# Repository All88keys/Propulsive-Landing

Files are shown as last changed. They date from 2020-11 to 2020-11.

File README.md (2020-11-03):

# propulsive-landing
 Arduino Script for HERMES rocket tests

## v0
Test scripts for LEMNOS3 board for Hermes I ("Agon0")

## v1
Test scripts for LEMNOS3 board for Hermes I ("Agon1")

## LEMNOS3
Autodesk EAGLE project for LEMNOS3, logic board design for Hermes I. 
- [Link to EAGLE download](https://www.autodesk.com/products/eagle/overview?plc=F360&term=1-YEAR&support=ADVANCED&quantity=1)
- [Link to MPU 6050](https://www.sparkfun.com/products/11028)

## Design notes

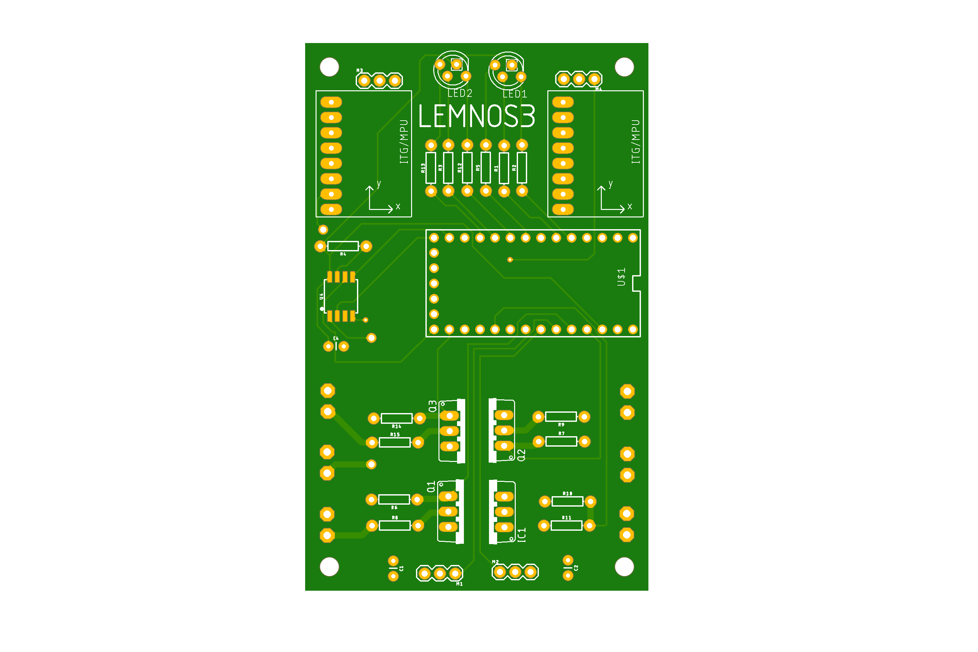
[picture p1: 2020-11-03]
LEMNOS3.png

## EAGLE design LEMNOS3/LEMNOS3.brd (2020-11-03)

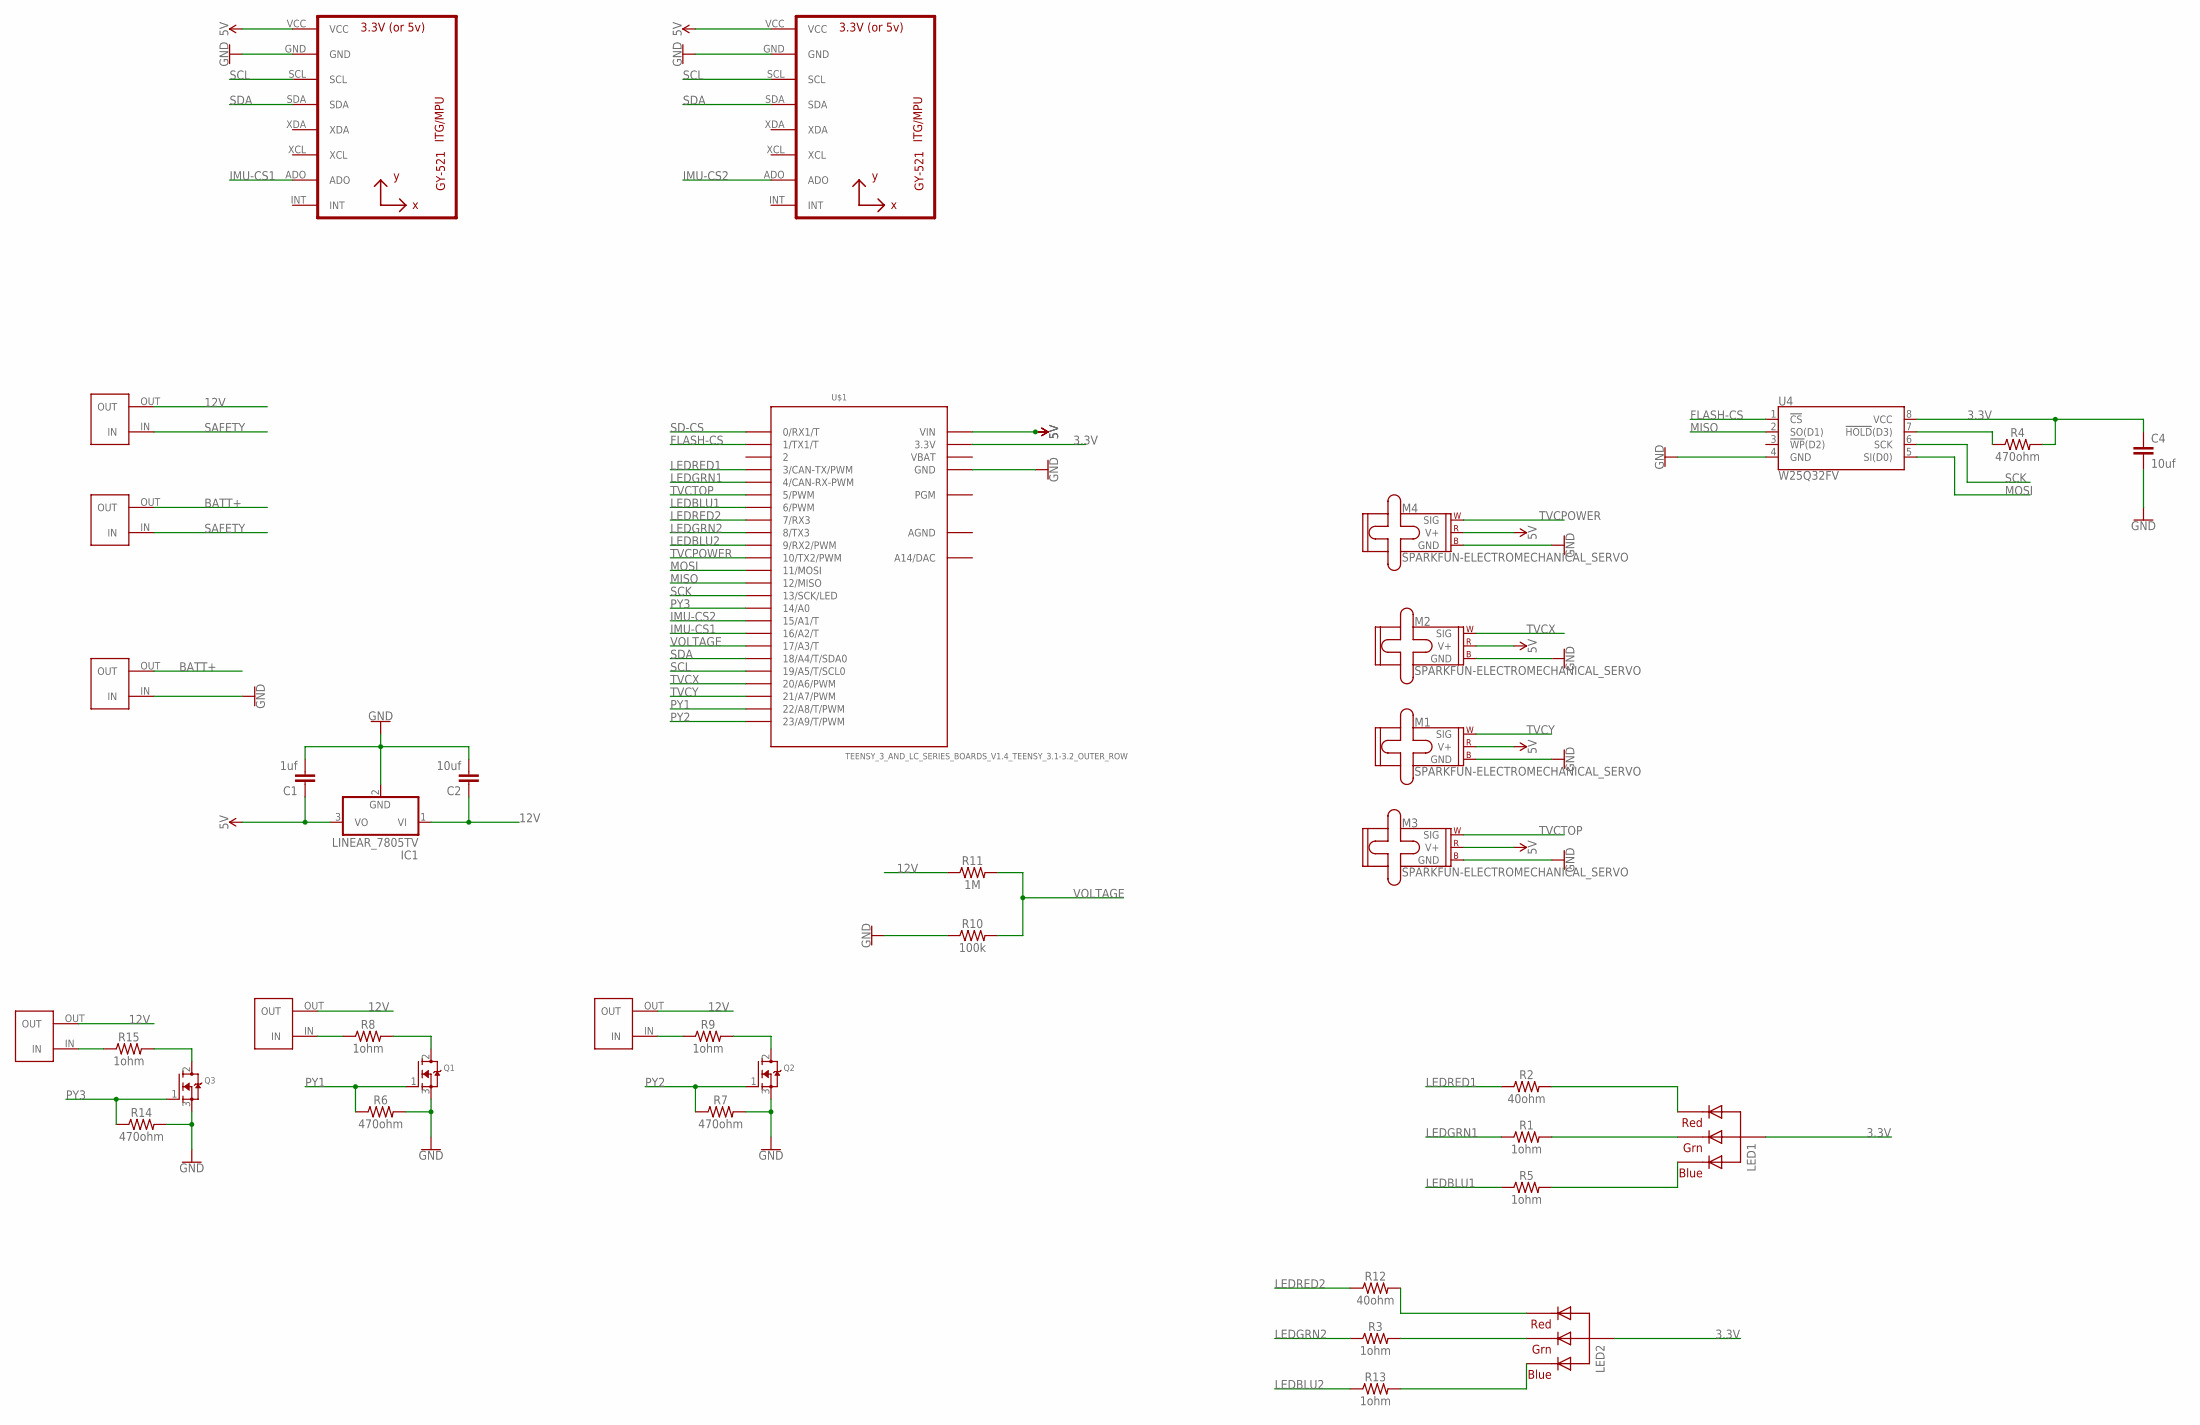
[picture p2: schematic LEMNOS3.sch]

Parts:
C1: 1uf; SPARKFUN-CAPACITORS_CAP-PTH-2.54
C2, C4: 10uf; SPARKFUN-CAPACITORS_CAP-PTH-2.54
IC1: LINEAR_7805TV; LINEAR_TO220V
LED1, LED2: RGBLED_CA-5MM; LED5MMRGB
M1, M2, M3, M4: SPARKFUN-ELECTROMECHANICAL_SERVO; SPARKFUN-ELECTROMECHANICAL_1X03
Q1, Q2, Q3: ADAFRUIT_MOSFET-NGDS_TO220V; ADAFRUIT_TO220V
R1, R3, R5, R8, R9, R13, R15: 1ohm; SPARKFUN-RESISTORS_AXIAL-0.3
R2, R12: 40ohm; SPARKFUN-RESISTORS_AXIAL-0.3
R4, R6, R7, R14: 470ohm; SPARKFUN-RESISTORS_AXIAL-0.3
R10: 100k; SPARKFUN-RESISTORS_AXIAL-0.3
R11: 1M; SPARKFUN-RESISTORS_AXIAL-0.3
U1, U2: GY-521_GY-521MPU6050; GY-521_GY-521
U4: W25Q32FV; SPARKFUN-IC-MEMORY_SOIC-8
U$1: TEENSY_3_AND_LC_SERIES_BOARDS_V1.4_TEENSY_3.1-3.2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; TEENSY_3_AND_LC_SERIES_BOARDS_V1.4_TEENSY_3.0-3.2&LC_OUTER_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
U$2, U$3, U$4, U$5, U$6, U$8: BLACKTERMBLOCK_BLACKTERMBLOCK

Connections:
3.3V: C4.1, LED1.2 (VCC), LED2.2 (VCC), R4.P$2 (2), U4.8 (VCC), U$1.3.3V, U$1.3.3V1 (3.3V)
5V: C1.1, IC1.3 (VO), M1.2 (V+), M2.2 (V+), M3.2 (V+), M4.2 (V+), U1.VCC, U2.VCC, U$1.VIN
12V: C2.1, IC1.1 (VI), R11.P$1 (1), U$2.OUT, U$5.OUT, U$6.OUT, U$8.OUT
AGND: U$1.AGND
BATT+: U$3.OUT, U$4.OUT
FLASH-CS: U4.1 (!CS!), U$1.1 (1/TX1/T)
GND: C1.2, C2.2, C4.2, IC1.2 (GND), M1.3 (GND), M2.3 (GND), M3.3 (GND), M4.3 (GND), Q1.3 (S), Q2.3 (S), Q3.3 (S), R6.P$2 (2), R7.P$2 (2), R10.P$1 (1), R14.P$2 (2), U1.GND, U2.GND, U4.4 (GND), U$1.GND, U$1.GND1 (GND), U$3.IN
IMU-CS1: U1.ADO, U$1.16/A2 (16/A2/T)
IMU-CS2: U2.ADO, U$1.15/A1 (15/A1/T)
LEDBLU1: R5.P$1 (1), U$1.6 (6/PWM)
LEDBLU2: R13.P$1 (1), U$1.9 (9/RX2/PWM)
LEDGRN1: R1.P$1 (1), U$1.4 (4/CAN-RX-PWM)
LEDGRN2: R3.P$1 (1), U$1.8 (8/TX3)
LEDRED1: R2.P$1 (1), U$1.3 (3/CAN-TX/PWM)
LEDRED2: R12.P$1 (1), U$1.7 (7/RX3)
MISO: U4.2 (SO(D1)), U$1.12 (12/MISO)
MOSI: U4.5 (SI(D0)), U$1.11 (11/MOSI)
unnamed: R15.P$1 (1), U$2.IN
unnamed: LED1.1 (RED), R2.P$2 (2)
unnamed: R4.P$1 (1), U4.7 (!HOLD!(D3))
unnamed: LED1.3 (GREEN), R1.P$2 (2)
unnamed: LED1.4 (BLUE), R5.P$2 (2)
unnamed: R8.P$1 (1), U$5.IN
unnamed: Q1.2 (D), R8.P$2 (2)
unnamed: LED2.1 (RED), R12.P$2 (2)
unnamed: R9.P$1 (1), U$6.IN
unnamed: Q2.2 (D), R9.P$2 (2)
unnamed: LED2.3 (GREEN), R3.P$2 (2)
unnamed: LED2.4 (BLUE), R13.P$2 (2)
unnamed: Q3.2 (D), R15.P$2 (2)
PY1: Q1.1 (G), R6.P$1 (1), U$1.22/A8 (22/A8/T/PWM)
PY2: Q2.1 (G), R7.P$1 (1), U$1.23/A9 (23/A9/T/PWM)
PY3: Q3.1 (G), R14.P$1 (1), U$1.14/A0
SAFETY: U$4.IN, U$8.IN
SCK: U4.6 (SCK), U$1.13 (13/SCK/LED)
SCL: U1.SCL, U2.SCL, U$1.19/A5 (19/A5/T/SCL0)
SD-CS: U$1.0 (0/RX1/T)
SDA: U1.SDA, U2.SDA, U$1.18/A4 (18/A4/T/SDA0)
TVCPOWER: M4.1 (SIG), U$1.10 (10/TX2/PWM)
TVCTOP: M3.1 (SIG), U$1.5 (5/PWM)
TVCX: M2.1 (SIG), U$1.20/A6 (20/A6/PWM)
TVCY: M1.1 (SIG), U$1.21/A7 (21/A7/PWM)
VBAT: U$1.VBAT
VOLTAGE: R10.P$2 (2), R11.P$2 (2), U$1.17/A3 (17/A3/T)

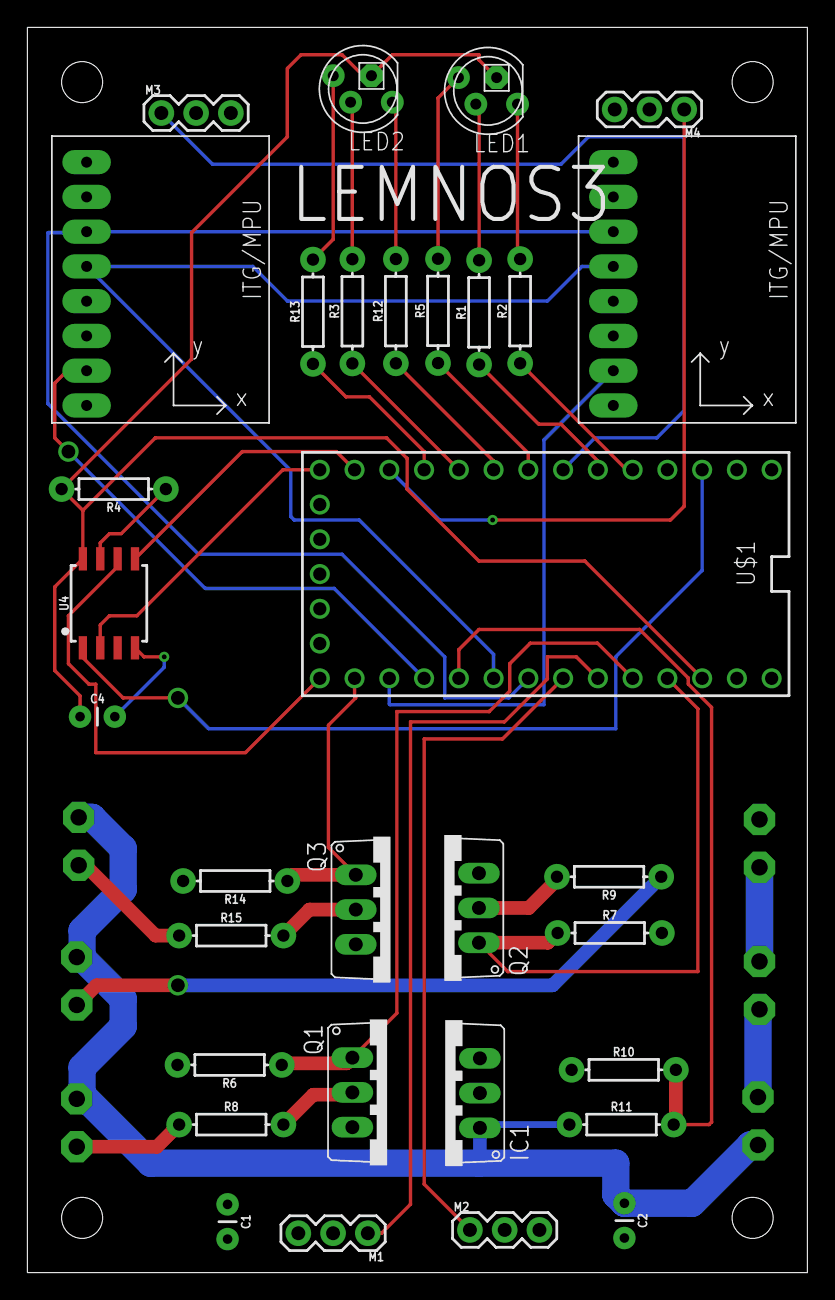
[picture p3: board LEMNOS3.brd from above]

Board: 2 copper layers, 57.0 x 91.0 mm, 38 parts (0 on the bottom side), 41 nets.

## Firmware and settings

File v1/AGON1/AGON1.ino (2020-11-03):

//includes
#include "I2Cdev.h"     //I2C protocol
#include "MPU6050.h"    //imu
#include "Wire.h"
#include <Eigen313.h>
//#include <stlport.h>
//#include <Eigen30.h>
using namespace Eigen;
#include <LU>
#include <SD.h>
#include<SPIFlash.h>
#include <Servo.h>

long MEGA=1000000;
long pi=31416;

//modes
int n=0;
int c=0;

//clock
long t0;
long t;
long h;

//mission parameters
long tb=.5*MEGA;
long tbEstDelay=.25*MEGA;
long setupWait=60; //120
long warningWait=60;  //120
long warning2Wait=30;  //30
long countdownWait=10; //10
long calibrateTime=0;

float dropTBuffer=.05*MEGA;
long dropBuffer=3276/8;  //~1 m/s^2
long dropGoal=-32768/8; //-g

float fireTBuffer=.05*MEGA;
float fireBuffer=3276/4/8; //~.25 m/s^2
float fireGoal=-32768/8; //-g

float landTBuffer=.5*MEGA;
float landBuffer=3276/2/8; //
float landGoal=0;

//mision variables
long dropT;
long dropTime;
long fireTime;
long landTime;
bool buffStatus;
float buffCountDown;
//float accAvg;
//float accCount;

//get accel, process y
int16_t ax, ay, az;
int16_t gx, gy, gz;
long offsets [3];
long O1, O2, O3;
int imuRange=32768;         //range of raw values that accelerometer will output
int aSensitivity=8;         //how many g's represented in that range
int gSensitivity=250;
float aMult=imuRange/9.81/aSensitivity;
//long gMult=imuRange/gSensitivity*180/pi*10000;
float gMult=imuRange/gSensitivity;
MPU6050 imu;
long yaw;

//controller
MatrixXf Ka(2,6);
VectorXi x(6); 
VectorXf xControl(6); 
VectorXf ua(2);
float ub [2];
float uc [2];
MatrixXi A [9];
MatrixXi B [9];
float maxU=5*3.14159/180;
long uLast [2]={0, 0};

//TVC
int TVC_TOP_PIN = 5;
int TVC_X_PIN = 20;
int TVC_Y_PIN = 21;
Servo tvcTop;
Servo tvcX;
Servo tvcY;
int tvcXoffset=85;
int tvcYoffset=83;
float beta=.6;
int gear=9;
float damper=1.5;
int tvcDelay=10;

//pyro
int pyroPin = 22;

//blink
int B_LED_1 = 6;
int G_LED_1 = 4;
int B_LED_2 = 9;
int G_LED_2 = 8;
//each pattern has 9 values
//0: Hz
//1-4: A, command for each, green1, blue1, green2, blue2,
//5-8: B, command for each
int blink0 [] ={1, 1, 0, 1, 0, 1, 0, 1, 0};
int blink1 [] ={1, 0, 1, 0, 1, 0, 1, 0, 1};
int blink2 [] ={1, 0, 1, 0, 1, 1, 0, 1, 0};
int blink3 [] ={1, 1, 0, 1, 0, 0, 0, 0, 0};
int blink4 [] ={1, 0, 0, 0, 0, 0, 0, 0, 0};
int blink5 [] ={1, 0, 1, 0, 1, 0, 1, 0, 1};
int blink6 [] ={1, 0, 0, 0, 0, 0, 0, 0, 0};
int blink7 [] ={1, 1, 0, 1, 0, 1, 0, 1, 0};
int blink8 [] ={1, 0, 1, 0, 1, 1, 0, 1, 0};
int blink9 [] ={1, 0, 1, 0, 1, 0, 1, 0, 1};
int blinkMaster [90];
int blinkCommand;
long nextBlink;
bool blinkFlag=false;

long dispGap=100000;
long nextDisplay=dispGap;

#define CHIPSIZE MB64
SPIFlash flash(1);


void setup() {

    pinMode(G_LED_1, OUTPUT);
    pinMode(B_LED_1, OUTPUT);
    pinMode(G_LED_2, OUTPUT);
    pinMode(B_LED_2, OUTPUT);
    
    digitalWrite(G_LED_1, LOW);
    digitalWrite(B_LED_1, LOW);
    digitalWrite(G_LED_2, LOW);
    digitalWrite(B_LED_2, LOW);
    
    // accel, processY
    // join I2C bus (I2Cdev library doesn't do this automatically)
    #if I2CDEV_IMPLEMENTATION == I2CDEV_ARDUINO_WIRE
        Wire.begin();
    #elif I2CDEV_IMPLEMENTATION == I2CDEV_BUILTIN_FASTWIRE
        Fastwire::setup(400, true);
    #endif
    

    flash.begin(9600);
    //flash.eraseChip();

    tvcX.attach(TVC_X_PIN);
    tvcY.attach(TVC_Y_PIN);
    tvcTop.attach(TVC_TOP_PIN);

    tvcTop.write(10); delay(1000);
    tvc(0, 0, beta, tvcDelay*100);
    tvc(30, 0, beta, tvcDelay*100);
    tvc(-30, 0, beta, tvcDelay*100);
    tvc(0, 0, beta, tvcDelay*100);
    tvc(0, 30, beta, tvcDelay*100);
    tvc(0, -30, beta, tvcDelay*100);
    tvc(0, 0, beta, tvcDelay*100);
    
    
  //blink
    for (int i=0; i<9; i++){
      blinkMaster[i+9*0]=blink0[i]; blinkMaster[i+9*1]=blink1[i];
      blinkMaster[i+9*2]=blink2[i]; blinkMaster[i+9*3]=blink3[i];
      blinkMaster[i+9*4]=blink4[i]; blinkMaster[i+9*5]=blink5[i];
      blinkMaster[i+9*6]=blink6[i]; blinkMaster[i+9*7]=blink7[i];
      blinkMaster[i+9*8]=blink8[i]; blinkMaster[i+9*9]=blink9[i];
    }

  pinMode(pyroPin, OUTPUT);
  digitalWrite(pyroPin, LOW);
    
  x<<0,0,0,0,0,0;
  Ka<<0.34641, 1.72254, 0.32694, 0, 0, 0, 0, 0, 0, 0.34641, -1.88376, -0.3991;
  n=0;
  t=0;
}

void loop() {

  //clk update
  
  t=micros();
  h=t-t0;
  t0=t;

  // check state
  switch(n){
    case 0: //setup and idle  &&& green
      if (t>setupWait*MEGA){
        n++; blinkFlag=true;
      }
    break;
    case 1: //warning  &&&   blue
      if (t>(setupWait+warningWait)*MEGA){
        n++; blinkFlag=true;
        //imu.CalibrateGyro(20);
        //imu.CalibrateAccel(50);
      }
    break;
    case 2: //clear the pad, calibrate   &&&   blue/green
      if (t>(setupWait+warningWait+warning2Wait)*MEGA){
        n++; blinkFlag=true;

          digitalWrite(G_LED_1, LOW);
          digitalWrite(B_LED_1, LOW);
          digitalWrite(G_LED_2, LOW);
          digitalWrite(B_LED_2, LOW);
          
          imu.initialize();
          imu.setFullScaleGyroRange(MPU6050_GYRO_FS_250);
          imu.setFullScaleAccelRange(MPU6050_ACCEL_FS_8);
          imu.CalibrateGyro(30); // Fine tune after setting offsets with less Loops.
          imu.CalibrateAccel(30);
      
          Serial.print(">");
          long aSums [3]={0,0,0};
          //float offsets
          for (int i=0; i<10; i++){
            for (int j=0; j<250; j++){
              imu.getMotion6(&ax, &az, &ay, &gx, &gz, &gy);
              aSums[0]+=ax;
              aSums[1]+=ay;
              aSums[2]+=az; 
      
            }
            Serial.print(".");
            delay(500);
          }
          Serial.println();
          for (int i=0; i<3; i++){
            aSums[i]/=2500;
            //Serial.println(aSums[i]);
          }
      
          offsets[0]=aSums[0];
          offsets[1]=aSums[1]-imuRange/2;
          offsets[2]=aSums[2];            

          calibrateTime=micros();
      }
    break;
    case 3: //countdown   &&&   green//off
      if (t>calibrateTime+countdownWait*MEGA){
        n++; blinkFlag=true;
        buffStatus=false; buffCountDown=dropTBuffer;
        tvcTop.write(150); delay(150);
        dropT=micros();
      }
    break;
    case 4: //drop   &&&   nothing
      if(az<dropGoal+dropBuffer){
        if (buffStatus){buffCountDown-=h; }
        else{buffStatus=true;}
      }
      else{
        if (buffStatus){buffStatus=false; buffCountDown=dropTBuffer; }
      }
      if ((buffCountDown<0) || (t>dropT+MEGA*.25)){
        dropTime=t-dropTBuffer;
        buffStatus=false; buffCountDown=dropTBuffer;
        //accAvg=0;accCount=0;
        n++; blinkFlag=true;
      }
    break;
    case 5: //ballistic (control tvc)   &&&  blue
      digitalWrite(pyroPin, HIGH);
      if (t>dropTime+tb-tbEstDelay){
        digitalWrite(pyroPin, HIGH);
        n++; blinkFlag=true; 
      }
    break;
    case 6: //fire pyros, check for accel   &&& nothing
      digitalWrite(pyroPin, HIGH);
      if(az>fireGoal+fireBuffer){
        if (buffStatus){buffCountDown-=h;}
        else{buffStatus=true;}
      }
      else{
        if (buffStatus){buffStatus=false; buffCountDown=fireTBuffer;}
      }
      if (buffCountDown<0){
        fireTime=t-fireTBuffer;
        buffStatus=false; buffCountDown=landTBuffer;
        //accAvg=0;accCount=0;
        n++; blinkFlag=true;
      }
    break;
    case 7: //tvc    &&& green
      digitalWrite(pyroPin, HIGH);
      if((az<landGoal+landBuffer) && (az>landGoal-landBuffer)){
        if (buffStatus){buffCountDown-=h;}
        else{buffStatus=true;}
      }
      else{
        if (buffStatus){buffStatus=false; buffCountDown=landTBuffer;}
      }
      if (buffCountDown<0){
        landTime=t-landTBuffer;
        n++; blinkFlag=true;
      }
    break;
    case 8: //land, turn off, transfer data     &&&     blue/green
      digitalWrite(pyroPin, LOW);
      //turn on leds
      //turn off stuff
      //transfer data
      blinkFlag=true;
    break;
  }
  if (n>2){
    c++;
    float Ox=x(4)*3.14/180/gMult/MEGA; 
    float Oy=x(1)*3.14/180/gMult/MEGA;
    float Oz=yaw*3.14/180/gMult/MEGA; 
  
    imu.getMotion6(&ax, &az, &ay, &gx, &gz, &gy);
    Serial.print(ax); Serial.print("\t");
    Serial.print(ay); Serial.print("\t");
    Serial.print(az); Serial.print("\t");
    Serial.print(gx); Serial.print("\t");
    Serial.print(gy); Serial.print("\t");
    Serial.print(gz); Serial.println("\t");
  
    ax=-ax+offsets[0];
    ay=-ay+offsets[1]+imuRange/2;
    az=az-offsets[2];
  
    
    
    Matrix3f bodyEuler;
    bodyEuler<< 1,0,-sin(Ox),0,cos(Oy),sin(Oy)*cos(Ox),0,-sin(Oy),cos(Oy)*cos(Ox);
    Vector3f deuler;
    deuler<<gx, gy, gz; deuler*=(-1);
    deuler=bodyEuler.inverse()*deuler;
    if (c>5){
    x(4)+=deuler(0)*h; x(1)+=deuler(1)*h; yaw+=deuler(2)*h;
    }
    x(5)=deuler(0); x(2)=deuler(1);
    
    MatrixXf R1(3,3); R1<<1, 0, 0, 0, cos(Ox), sin(Ox), 0, -sin(Ox), cos(Ox);
    MatrixXf R2(3,3); R2<<cos(Oy), 0, -sin(Oy), 0, 1, 0, sin(Oy), 0, cos(Ox);
    MatrixXf R3(3,3); R3<<cos(Oz), sin(Oz), 0, -sin(Oz), cos(Oz), 0, 0, 0, 1;
    MatrixXf R(3,3); R=R1*R2*R3; 
    Vector3f ve; ve<<ax, ay, az;
    ve=R*ve;
    if (c>10){
      x(0)+=ve[0]*h; x(3)+=ve[1]*h;
    }
  
    xControl(0)=x(0)/aMult/MEGA/50;
    xControl(3)=x(3)/aMult/MEGA/50;
    xControl(1)=x(1)/gMult/MEGA/180*3.14;
    xControl(4)=x(4)/gMult/MEGA/180*3.14;
    xControl(2)=x(2)/gMult/180*3.14;
    xControl(5)=x(5)/gMult/180*3.14;
  
    ua=-Ka*xControl;
    
    float uNorm=sqrt(ua(0)*ua(0)+ua(1)*ua(1));
    //Serial.print("     "); Serial.print(uNorm); Serial.print("     "); Serial.println(maxU);
    if (uNorm>maxU){
      //Serial.print("TRUE  ");
      ub[0]=ua(0)/uNorm*maxU;
      ub[1]=ua(1)/uNorm*maxU;
    }
    else {
      ub[0]=ua(0); ub[1]=ua(1);
    }
  
    uc[0]=(ub[0])*cos(Oz)+(ub[1])*sin(Oz);
    uc[1]=(ub[1])*cos(Oz)-(ub[0])*sin(Oz);
  
    //Serial.print(u(0)); Serial.print("\t"); 
    //Serial.println(u(1));
    
    if((n>3)&(n<8)){
      int x=uc[0]*180*gear/3.14;
      int y=uc[1]*180*gear/3.14;
      bool newU=((x!=uLast[0]) || (y!=uLast[1]));
      if (newU){
        tvc(x, y, beta, tvcDelay);
        uLast[0]=x; uLast[1]=y;
      }
    }
    
    
    
    //Serial.print(xControl(1)); Serial.print("\t");
    //Serial.println(xControl(4));
  }

  //blink
  if ((t>nextBlink)||(blinkFlag)){
    blinkFlag=false;
    //if (blinkCommand==1) {blinkCommand=0;} else {blinkCommand=1;}
    blinkCommand=~blinkCommand;
    if (blinkMaster[9*n-4*blinkCommand+1]){
      digitalWrite(B_LED_1, LOW);
    }
    else{
      digitalWrite(B_LED_1, HIGH);
    }
    if (blinkMaster[9*n-4*blinkCommand+2]){
      digitalWrite(G_LED_1, LOW);
    }
    else{
      digitalWrite(G_LED_1, HIGH);
    }
    if (blinkMaster[9*n-4*blinkCommand+3]){
      digitalWrite(B_LED_2, LOW);
    }
    else{
      digitalWrite(B_LED_2, HIGH);
    }
    if (blinkMaster[9*n-4*blinkCommand+4]){
      digitalWrite(G_LED_2, LOW);
    }
    else{
      digitalWrite(G_LED_2, HIGH);
    }
    nextBlink=t+MEGA/blinkMaster[9*n];
  }

  if (n>2){
    void record();
  }


}

void tvc(int x, int y, double gamma, int d){
  double u=(x)*cos(gamma)+(y)*sin(gamma);
  double v=(y)*cos(gamma)-(x)*sin(gamma);
  if (u-uLast[0]>2){
    u=uLast[0]+2;
  }
  else if (u-uLast[0]<-2){
    u=uLast[0]-2;
  }

  if (v-uLast[1]>2){
    v=uLast[1]+2;
  }
  else if (v-uLast[1]<-2){
    v=uLast[1]-2;
  }
  uLast[0]=u; uLast[1]=v;
  tvcY.write(v+tvcYoffset);tvcX.write(u+tvcXoffset); delay(d);
}

void record(){
  long dataL [17]={n, t, ax, ay, az, gx, gy, gz, x(0), x(1), x(2), x(3), x(4), x(5), yaw, uLast[0], uLast[1]};
  float dataF [12]={xControl(0), xControl(1), xControl(2), xControl(3), xControl(4), xControl(5), ua(0), ua(1), ub[0], ub[1], uc[0], uc[1]};
  bool newPoint[4]={false, false, false, false};

  
  uint32_t floatAddr [12];
  uint32_t longAddr [17];
  uint32_t newPointAddr[4];
  bool success;

  for (uint32_t i = 0; i < arrayLen(newPointAddr); i++) {
    newPointAddr[i] = flash.getAddress(sizeof(bool));
    success=flash.writeLong(newPointAddr[i], newPoint[i]);
    if (!success){
      Serial.println("flashFail");
    }
  }
  for (uint32_t i = 0; i < arrayLen(longAddr); i++) {
    longAddr[i] = flash.getAddress(sizeof(long));
    success=flash.writeLong(longAddr[i], dataL[i]);
    if (!success){
      Serial.println("flashFail");
    }
  }
  for (uint32_t i = 0; i < arrayLen(floatAddr); i++) {
    floatAddr[i] = flash.getAddress(sizeof(float));
    success=flash.writeFloat(floatAddr[i], dataF[i]);
  }

  
}

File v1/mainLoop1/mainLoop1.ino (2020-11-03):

//includes
#include "I2Cdev.h"     //I2C protocol
#include "MPU6050.h"    //imu
#include "Wire.h"
#include <Eigen313.h>
//#include <stlport.h>
//#include <Eigen30.h>
using namespace Eigen;
#include <SD.h>
#include<SPIFlash.h>
#include <Servo.h>

long MEGA=1000000;
long pi=31415;

//get accel, process y
int16_t ax, ay, az;
int16_t gx, gy, gz;
int imuRange=32768;         //range of raw values that accelerometer will output
int aSensitivity=8;   //how many g's represented in that range
int gSensitivity=250;
long lastAcc [6];
long aMult=imuRange/9.81/aSensitivity;
long gMult=imuRange/gSensitivity;
MPU6050 imu;
MatrixXi bodyEuler(3,3);
MatrixXi R1(3,3);
MatrixXi R2(3,3);
MatrixXi R3(3,3);

//controller
float KABiterTimes [9];
int KABcount;
MatrixXi K(2, 6) [9];
VectorXi x(6);
VectorXi u(2);
VectorXi dx(6);
MatrixXi A [9];
MatrixXi B [9];
long maxU=5*MEGA/10000*pi/180;

//yaw
long yaw;
long lastyaw;

//observer
MatrixXi L(6,4);
MatrixXi C(4,6);
//initialize C<<1, 0, 0, 0, 0, 0....;
VectorXi y(4);

//modes
int n=0;

//clock
long t0;
long t;
long h;

//mission parameters
long tb;
long tbEstDelay;
long setupWait=600;
long warningWait=240;
long warning2Wait=50;
long countdownWait=10;

float dropTBuffer=.1;
float dropBuffer=1;
float dropGoal=-9.81;

float fireTBuffer=.1;
float fireBuffer=.25;
float fireGoal=-9.81;

float landTBuffer=1.5;
float landBuffer=.5;
float landGoal=0;

//mision variables
long dropTime;
long fireTime;
long landTime;
bool buffStatus;
float buffCountDown;
//float accAvg;
//float accCount;


//blink
int B_LED_1 = 6;
int G_LED_1 = 4;
int B_LED_2 = 9;
int G_LED_2 = 8;
//each pattern has 9 values
//0: Hz
//1-4: A, command for each, green1, blue1, green2, blue2,
//5-8: B, command for each
int blink0 [] ={1, 1, 0, 1, 0, 1, 0, 1, 0};
int blink1 [] ={1, 0, 1, 0, 1, 0, 1, 0, 1};
int blink2 [] ={1, 0, 1, 0, 1, 1, 0, 1, 0};
int blink3 [] ={1, 1, 0, 1, 0, 0, 0, 0, 0};
int blink4 [] ={1, 0, 0, 0, 0, 0, 0, 0, 0};
int blink5 [] ={1, 0, 1, 0, 1, 0, 1, 0, 1};
int blink6 [] ={1, 0, 0, 0, 0, 0, 0, 0, 0};
int blink7 [] ={1, 1, 0, 1, 0, 1, 0, 1, 0};
int blink8 [] ={1, 0, 1, 0, 1, 1, 0, 1, 0};
int blink9 [] ={1, 0, 1, 0, 1, 0, 1, 0, 1};
int * blinkMaster;
int blinkCommand;
long nextBlink;
bool blinkFlag=false;

//sd card
Sd2Card card;
SdVolume volume;
SdFile root;
const int SDchipSelect = 0;

//flash
#define CHIPSIZE MB64
SPIFlash flash(1);

//record
long dp [31];
String sBegin="begin     ";
String sEnd="     end";
String newPoint="n";
String sModeSwitch="";
uint32_t dpAddr;

//TVC
int TVC_TOP_PIN = 5;
int TVC_X_PIN = 20;
int TVC_Y_PIN = 21;
Servo tvcTop;
Servo tvcX;
Servo tvcY;


void setup() {
  
  delay(2000);

  //blink
    blinkMaster=new int[9*10];
    pinMode(G_LED_1, OUTPUT);
    pinMode(B_LED_1, OUTPUT);
    pinMode(G_LED_2, OUTPUT);
    pinMode(B_LED_2, OUTPUT);
  
  // accel, processY
    // join I2C bus (I2Cdev library doesn't do this automatically)
    #if I2CDEV_IMPLEMENTATION == I2CDEV_ARDUINO_WIRE
        Wire.begin();
    #elif I2CDEV_IMPLEMENTATION == I2CDEV_BUILTIN_FASTWIRE
        Fastwire::setup(400, true);
    #endif
    //initialize serial
    Serial.begin(38400);
    //initialize peripherals
    imu.initialize();
    imu.setFullScaleGyroRange(MPU6050_GYRO_FS_250);
    imu.setFullScaleAccelRange(MPU6050_ACCEL_FS_8);
    imu.CalibrateGyro(10);
    imu.CalibrateAccel(25);
    
    flash.begin(9600);
}

void loop() {
  
  //clk update
  t=micros();
  h=t-t0;
  t0=t;
  
  // check state
  switch(n){
    case 0: //setup and idle  &&& green
      if (t>setupWait*MEGA){
        n++; blinkFlag=true;
      }
    break;
    case 1: //warning  &&&   blue
      if (t>(setupWait+warningWait)*MEGA){
        n++; blinkFlag=true;
        imu.CalibrateGyro(20);
        imu.CalibrateAccel(50);
      }
    break;
    case 2: //clear the pad, calibrate   &&&   blue/green
      if (t>(setupWait+warningWait+warning2Wait)*MEGA){
        n++; blinkFlag=true;
      }
    break;
    case 3: //countdown   &&&   green//off
      accAvg+=az/MEGA;
      accCount++;
      if (t>(setupWait+warningWait+warning2Wait+countdownWait)*MEGA){
        //turn top servo
        n++; blinkFlag=true;
        buffStatus=false; buffCountDown=dropTBuff;
      }
    break;
    case 4: //drop   &&&   nothing
      if(ddz<accAvg/accCount-dropBuff){
        if (buffStatus){buffCountDown-=h;}
        else{buffStatus=true;}
      }
      else{
        if (buffStatus){buffStatus=false; buffCountDown=dropTBuff;}
      }
      if (buffCountDown<0){
        dropTime=t-dropTBuffer;
        buffStatus=false; buffCountDown=dropTFire;
        accAvg=0;accCount=0;
        n++; blinkFlag=true;
      }
    case 5: //ballistic (control tvc)   &&&  blue
      accAvg+=az/MEGA;
      accCount++;
      if (t>dropTime+tb-tbEstDelay){
        //fire pyros
        n++; blinkFlag=true;
      }
    break;
    case 6: //fire pyros, check for accel   &&& nothing
      if(ddz>accAvg/accCount+fireBuff){
        if (buffStatus){buffCountDown-=h;}
        else{buffStatus=true;}
      }
      else{
        if (buffStatus){buffStatus=false; buffCountDown=fireTBuff;}
      }
      if (buffCountDown<0){
        fireTime=t-fireTBuffer;
        buffStatus=false; buffCountDown=landTFire;
        accAvg=0;accCount=0;
        n++; blinkFlag=true;
      }
    break;
    case 7: //tvc    &&& green
      digitalWrite(G_LED_1, LOW);
      digitalWrite(G_LED_2, LOW);
      digitalWrite(B_LED_1, HIGH);
      digitalWrite(B_LED_2, HIGH);
      if((ddz+landBuff<landGoal) && (ddz-landBuff>landGoal)){
        if (buffStatus){buffCountDown-=h;}
        else{buffStatus=true;}
      }
      else{
        if (buffStatus){buffStatus=false; buffCountDown=landTBuff;}
      }
      if (buffCountDown<0){
        landTime=t-landTBuffer;
        n++; blinkFlag=true;
      }
    break;
    case 8: //land, turn off, transfer data     &&&     blue/green
      digitalWrite(G_LED_1, HIGH);
      digitalWrite(G_LED_2, HIGH);
      digitalWrite(B_LED_1, LOW);
      digitalWrite(B_LED_2, LOW);
      //turn on leds
      //turn off stuff
      //transfer data
      n++; blinkFlag=true;
    break;
    case 9: //ready to turn off         &&&     blue
      digitalWrite(G_LED_1, HIGH);
      digitalWrite(G_LED_2, HIGH);
      digitalWrite(B_LED_1, HIGH);
      digitalWrite(B_LED_2, HIGH);
      while(1){}
    break;
  }

  if ((n>1) & (n<9)){

    //iterKAB
    if (n==5) {KABcount=1;}
    else if (n>5){
      if ((t>tb+KABiterTimes[KABcount+1]*MEGA)&(KABcount<9)){KABcount++;}
    }
    
    dp[0]=t; dp[1]=n; 
    
    //get accel
    imu.getMotion6(&ax, &ay, &az, &gx, &gy, &gz);
    
    dp[2]=ax; dp[3]=ay; dp[4]=az; dp[5]=gx; dp[6]=gy;  dp[7]=gz;
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

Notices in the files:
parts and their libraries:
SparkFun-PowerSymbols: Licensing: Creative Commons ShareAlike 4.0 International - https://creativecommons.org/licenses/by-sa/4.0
